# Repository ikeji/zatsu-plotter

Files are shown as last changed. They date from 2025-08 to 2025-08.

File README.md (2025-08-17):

# 雑プロッタ

コンピュータを使って物理的な機械を動かしたい。
今回は、ペンを設定した通り動かすペンプロッタを作りたい。

既存の作例は、リニアレールを使ったり既存の直動機構を使ったり、
専用の部品を使って精度高く作ってあるものが多い。

今回は、誰の家にもありそうな、汎用の部品と、
3Dプリンタで印刷したもの、
あとは100円ショップで買えるものを組み合わせて組む事で、
肩肘立てずに適当に作れる事を目標にした。

## 用意するもの

3つのグループの物が必要。

### 通販で買った物

今回のために特別に買ったのではなく、家に落ちてたものを使った。

- RaspberryPi Pico (もしくは互換ボード) 1つ 300円ぐらい
- 28BYJ-48ステッピングモータ 2つ 制御基板つきのもの 200円ぐらい
- M3 ボルトナットセット 500円ぐらい
- ジャンパワイヤ
- ブレットボード

自分はどれもAliexpressで買った。
国内の通販でも買えると思う。

### ダイソーで買った物 660円ぐらい

- バインダー 
- 凧糸 
- 太さ3mmのたけひご 
- ボールペン
- はさみ
- ねじまわし

プラスチックのバインダーはポリカーネート製で、厚さが2mmあった。

ペンはゴムの持ち手がついてない方がよさそう。
鉛筆でもいいかも。

### 3Dプリンタで印刷したもの

- (A)[プーリー](./step/a-pully.step) 8つ 
- (B)[プーリークリップ](./step/b-pully-clip.step) 2つ 
- (C)[プーリー軸](./step/c-pully-axis.step) 2つ 
- (D)[モータークリップ](./step/d-motor-clip.step) 2つ 
- (E)[モーター用プーリー](./step/e-motor-pully.step) 2つ 
- (F)[Xブロック](./step/f-x-block.step) 2つ 
- (G)[Xブロック軸](./step/g-x-block-cap.step) 2つ 
- (H)[ヘッド](./step/h-head.step) 1つ 

FreeCADでデザインした。

自分はBambuLabのP1Sで印刷したが、
だいたいのプリンタでは印刷できると思う。

このプロッタを作りたいけど、
3Dプリンタがなくて困ってるという人は、
日本国内の住所を教えてくれたら郵便で送ります。

## モジュールの組み立て

### 2連プーリーモジュール

(B)プーリークリップには、ナットを入れる所が2箇所があるので押し込む。
反対からボルトを入れて締めると入れやすい。

(C)プーリー軸にも2箇所に入れるところがあるので入れる。
裏表に注意



(A)プーリーを挟んで8mmのネジと10mmのネジで組み立てる。



### モーターモジュール

28BYJ-48モータを(D)モータクリップにつける。
5mmのボルトで止める。

モータの軸に(E)モータ用プーリーをつける。
抜けないようにキツめに作ってあるので、
がんばって押し込む。




### Xモジュール

まず、2連プーリーモジュールと同じ感じで組み立てる。

(F)Xブロックに2個、(G)X軸に2つナットを入れる。



左右のブロックをたけひごでつなぐ。
モジュール全体の長さがバインダーの幅と同じになるように調整したい。
たけひごはバインダーの幅から1cm減らした長さに切る。




### ヘッド

裏にナット4つをつける。
表に5mmのボルトを入れる。



ペンを付けられるように20mmのボルトとナットをつける。



## 全体の組み立てと糸張り

### 四隅のモジュールの固定

バインダーの四隅にプーリーモジュールとモーターモジュールを挟む。
裏返して、紐をまわして縛る。
これで、バインダーにモジュールを固定してる。




### 糸張り

Xモジュールとヘッドを置き、糸をはわせる。

次の図を参照



1本の糸で、1-14まで順番に通す。
糸がピンと張るようにして、糸の両端をネジで止める。

中間(7と8の間)のネジはゆるめておき、
たけひごとヘッドが、水平になるように調整し中間をネジで止める。



## 配線

モータを制御基板を経由してマイコンにつなぐ。
左のモータをマイコンの0-3ピン、
右のモータをマイコンの4-7ピンにつないだ。

制御基板の電源をマイコンのVCCとGNDにつなぐ。
自分は分配にブレッドボードを使った。

## ソフトウエア

自分はMicroPythonで制御した。

MicroPythonのサイトからU2Fをダウンロードし、
RaspberryPiに入れる。

次に用意したサンプルスクリプト([sample.py](./firmware/sample.py))を書き込む。
Linuxならmpremoteコマンドを使ってる。
このスクリプトは設定した四角形を描く。

## しくみ

このプロッタはCoreXY方式を使っている。

左右のモーターを同じ方向にまわすとヘッドが左右に動く。
例えば、両方のモータを反時計回りに動かすと、ヘッドは右に動く。



モーターを左右で逆の方向に動かすとヘッドが上下に動く。
例えば、左のモータを反時計まわり、右のモータを時計まわりに動かすと、
ヘッドは上に動く。



## リンク

- 動画
  - [第一世代](https://x.com/ikeji/status/1926441077013106829)
  - [第二世代](https://x.com/ikeji/status/1931363801653526600)
- 開発ログ
  - [2025W21](https://blog.ikejima.org/weekly/2025/05/26/2025w21.html)
  - [2025W22](https://blog.ikejima.org/weekly/2025/06/03/2025w22.html)
  - [2025W23](https://blog.ikejima.org/weekly/2025/06/10/2025w23.html)
- 紹介された
  - [2025年4-6月の自作ペンプロッタを愛でる会](https://note.com/penplotter/n/n4fdf6959738a#017fe1ae-cd83-49cf-acd3-3303a340d920)

## 免責事項

無保証/MIT License

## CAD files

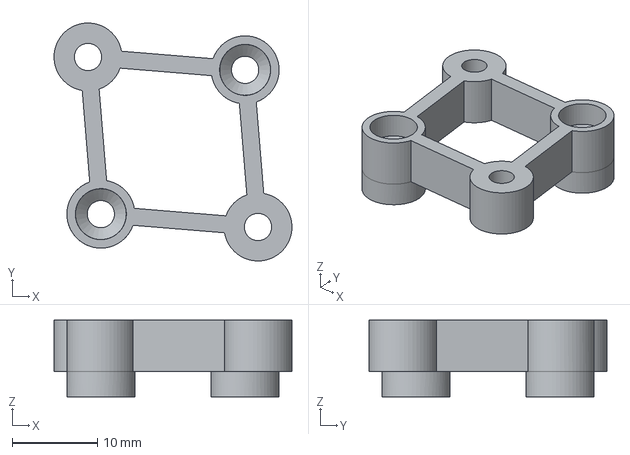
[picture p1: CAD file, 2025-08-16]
step/c-pully-axis.step
28.0 x 28.0 x 9.00 mm

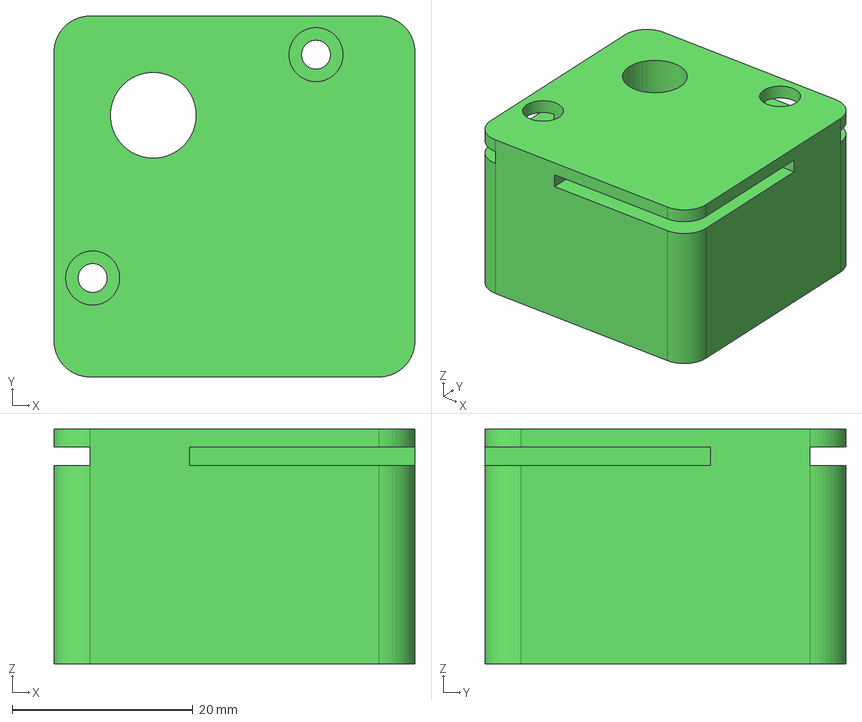
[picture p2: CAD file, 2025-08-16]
step/d-motor-clip.step
40.0 x 40.0 x 26.0 mm

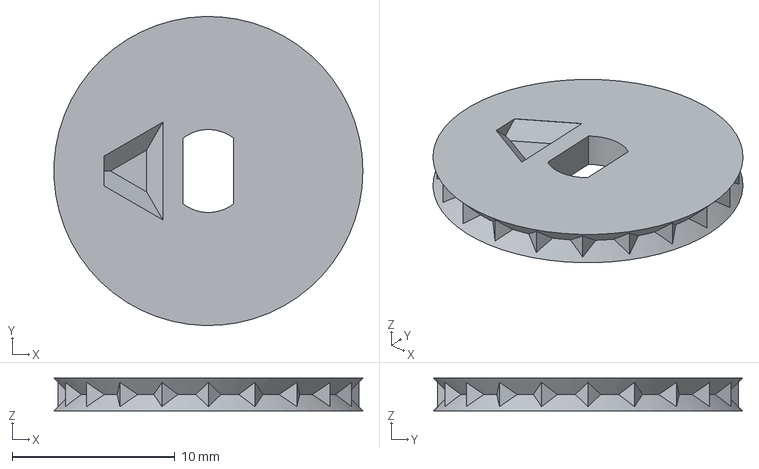
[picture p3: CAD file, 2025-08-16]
step/e-motor-pully.step
19.0 x 19.0 x 2.00 mm

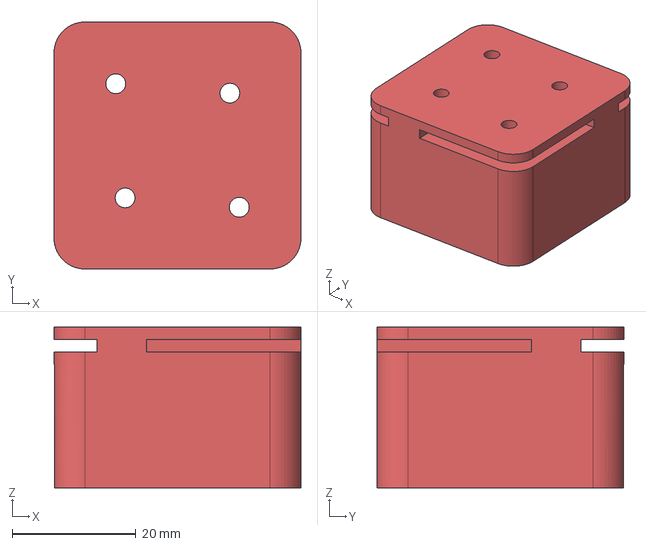
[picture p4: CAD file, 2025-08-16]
step/b-pully-clip.step
40.0 x 40.0 x 26.0 mm

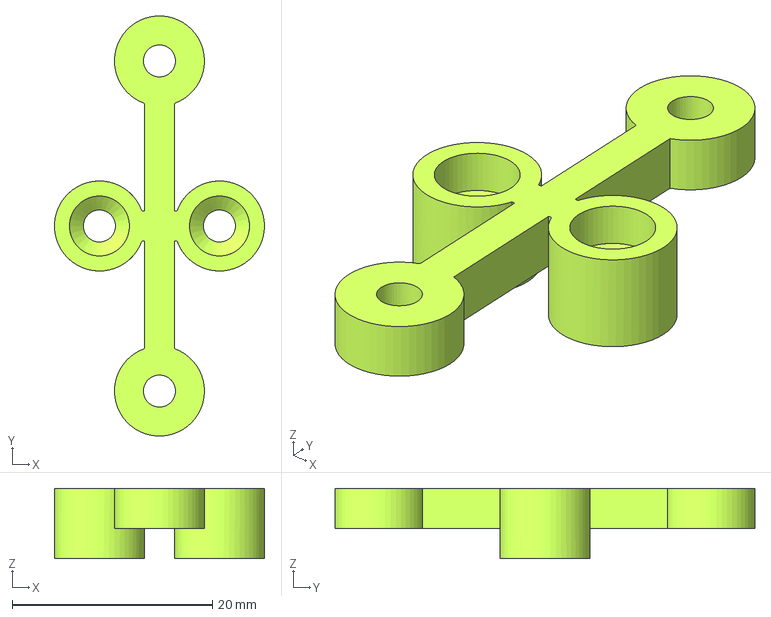
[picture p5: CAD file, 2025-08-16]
step/g-x-block-cap.step
21.0 x 42.0 x 7.00 mm

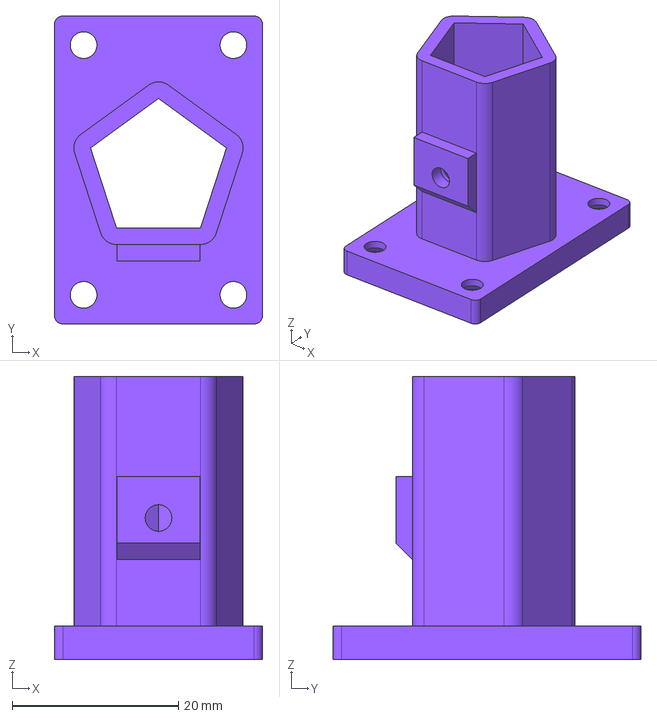
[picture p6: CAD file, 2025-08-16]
step/h-head.step
25.0 x 37.0 x 34.0 mm

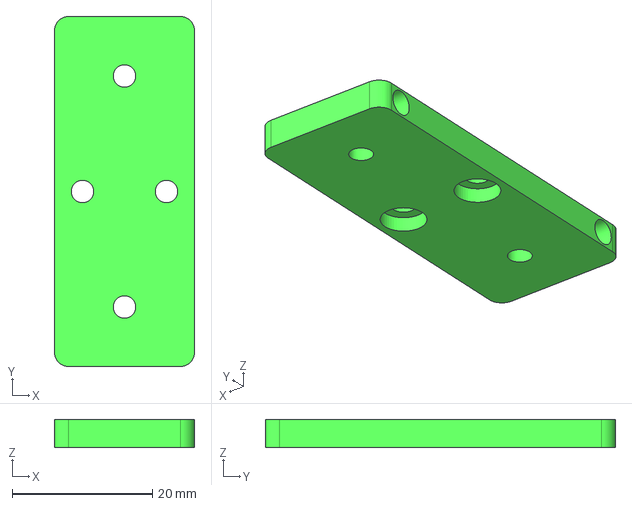
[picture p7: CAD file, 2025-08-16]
step/f-x-block.step
20.0 x 50.0 x 4.00 mm

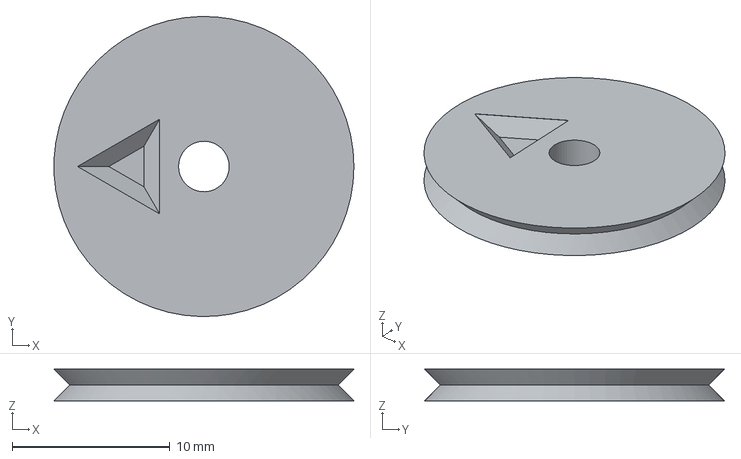
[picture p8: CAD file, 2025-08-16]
step/a-pully.step
19.0 x 19.0 x 2.00 mm

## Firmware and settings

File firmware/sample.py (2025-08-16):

from machine import Pin
from time import sleep_ms

pin1 = Pin(0,Pin.OUT)
pin2 = Pin(1,Pin.OUT)
pin3 = Pin(2,Pin.OUT)
pin4 = Pin(3,Pin.OUT)
pin5 = Pin(4,Pin.OUT)
pin6 = Pin(5,Pin.OUT)
pin7 = Pin(6,Pin.OUT)
pin8 = Pin(7,Pin.OUT)

class BYJ:
    def __init__(self, pins):
        self.pins = pins
        self.current_phase = 0

    def step(self):
        self.current_phase = (self.current_phase + 1) % 4
        self._update()
    def unstep(self):
        self.current_phase = (self.current_phase - 1 + 4) % 4
        self._update()

    def _update(self):
        for i in range(4):
            self.pins[i].value(i==self.current_phase)

# 左のモータ
byj1 = BYJ([pin1, pin2, pin3, pin4])
# 右のモータ
byj2 = BYJ([pin5, pin6, pin7, pin8])

# ヘッドを左に動かす。
def left(steps):
    for i in range(steps):
        byj1.step()
        byj2.step()
        sleep_ms(4)

# ヘッドを右に動かす。
def right(steps):
    for i in range(steps):
        byj1.unstep()
        byj2.unstep()
        sleep_ms(4)

# ヘッドを上に動かす。
def up(steps):
    for i in range(steps):
        byj1.unstep()
        byj2.step()
        sleep_ms(4)

# ヘッドを下に動かす。
def down(steps):
    for i in range(steps):
        byj1.step()
        byj2.unstep()
        sleep_ms(4)

# 四角を描画
def square():
    up(1000)
    left(1000)
    down(1000)
    right(1000)

square()
